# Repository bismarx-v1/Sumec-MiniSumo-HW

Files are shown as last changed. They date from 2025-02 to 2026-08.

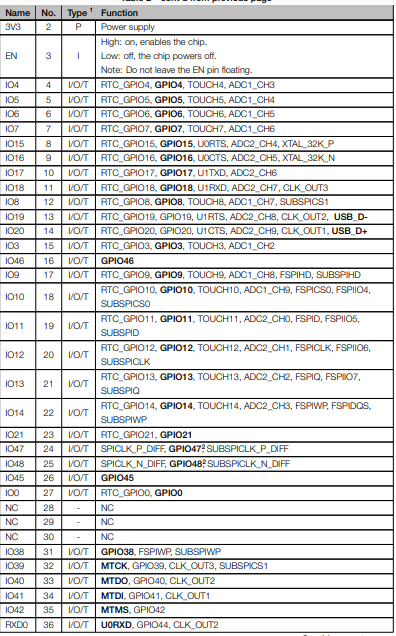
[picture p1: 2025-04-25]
main_hw/SUMEC_MK_II/REF. images/S3 pinout 1.png

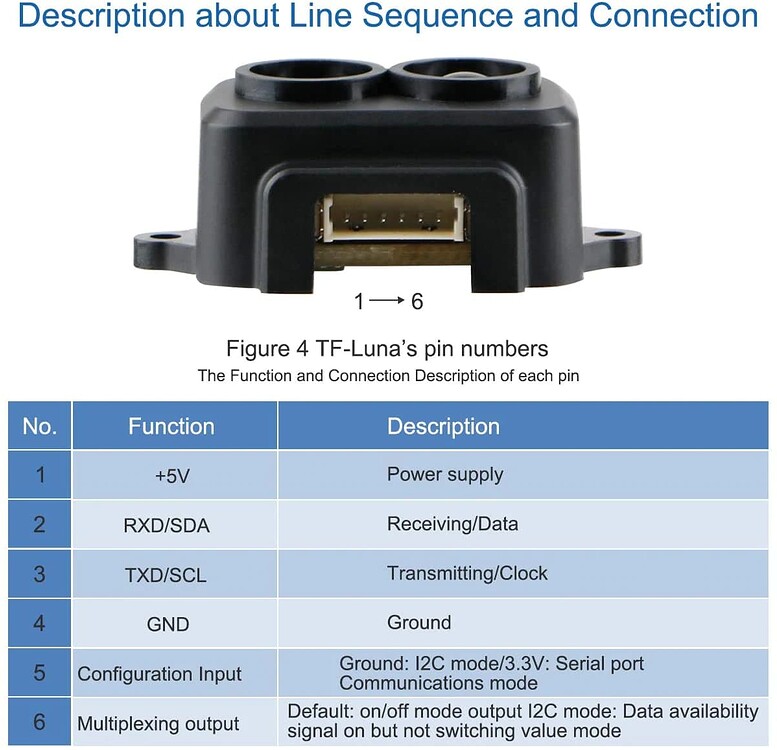
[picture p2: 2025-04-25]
main_hw/SUMEC_MK_II/REF. images/TF-Luna pinout.jpeg

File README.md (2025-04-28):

# SUMEC - HARDWARE - ELECTRONICS

**SUMEC** - is an autonomous MiniSumo robot, that is designed to compete in MiniSumo competitions. MiniSumo robots are small 100mmx100mm autonomous robots that combine electronics, software and mechanics into one project, their task it to push their opponent out of a ring. This project is led and managed by [SPŠ na Proseku](https://www.sps-prosek.cz) students.

## Table of Contents
- Description
- Contents
- Contributors
- Our Suppliers
- Contact
- Acknowledgements

## Description
This GitHub repository contains PCB files, gerber plots and main electronics used by SUMEC MiniSumo robot.

## Contents
- **main_hw**: Includes schematics and PCB files for the main board, production files such as Gerber plots and BOMs, .step files of the board, and PDF plots.
- **libs**: Contains needed libraries such as the footprint folder, 3D files in .step format, and the symbol library for schematics.

## Contributors
**HARDWARE Repository Supervisor**:
- **Savva Popov** - Head Hardware Developer and PCB Designer

**Project Contributors**:
- **Antonín Havlík** - Head Software Developer
- **Šimon Šťastný** - Head Mechanical Designer and Developer
- **Jonáš Jarý** - Mechanical Developer, Software and Hardware Development Assistant
- **Lukáš Houdek** - Mechanical Designer and Developer, 3D Printing Expert
- **Roselyn Natani Šimáčková** - Software developer, head functions developer

## Our Suppliers
We buy our components from:
- Mouser Electronics
- GM Electronics
- TME
- BotLand

## Contact
If you have any questions, suggestions, or issues regarding this project or repository, please feel free to contact:

### **Savva Popov** - Head Hardware Developer
  - Email: savva.popov.sp@gmail.com
  - LinkedIn: [Savva Popov](https://www.linkedin.com/in/savva-popov/)

### Other Contacts:
- **Antonín Havlík** - Head Software Developer
  - Email: [HAVLIK EMAIL]
- **Šimon Šťastný** - Head Mechanical Designer and Developer
  - Email: simon.ststn@gmail.com
- **Jonáš Jarý** - Mechanical Developer, Software and Hardware Development Assistant
  - Email: jary.jonas@gmail.com
- **Lukáš Houdek** - Mechanical Designer and Developer, 3D Printing Expert
  - Email: [HOUDEK EMAIL]
- **Roselyn Natani Šimáčková** - Software Developer, Head functions developer
  - Email: [SIMACKOVA EMAIL]

## Acknowledgements
We would like to thank Ing. Jaroslav Bušek PhD, for providing contacts and mentoring during the development of this project, and our school SPŠ na Proseku for providing workplace, knowledge, and top-notch equipment.

**Sending love from the Czech Republic!**

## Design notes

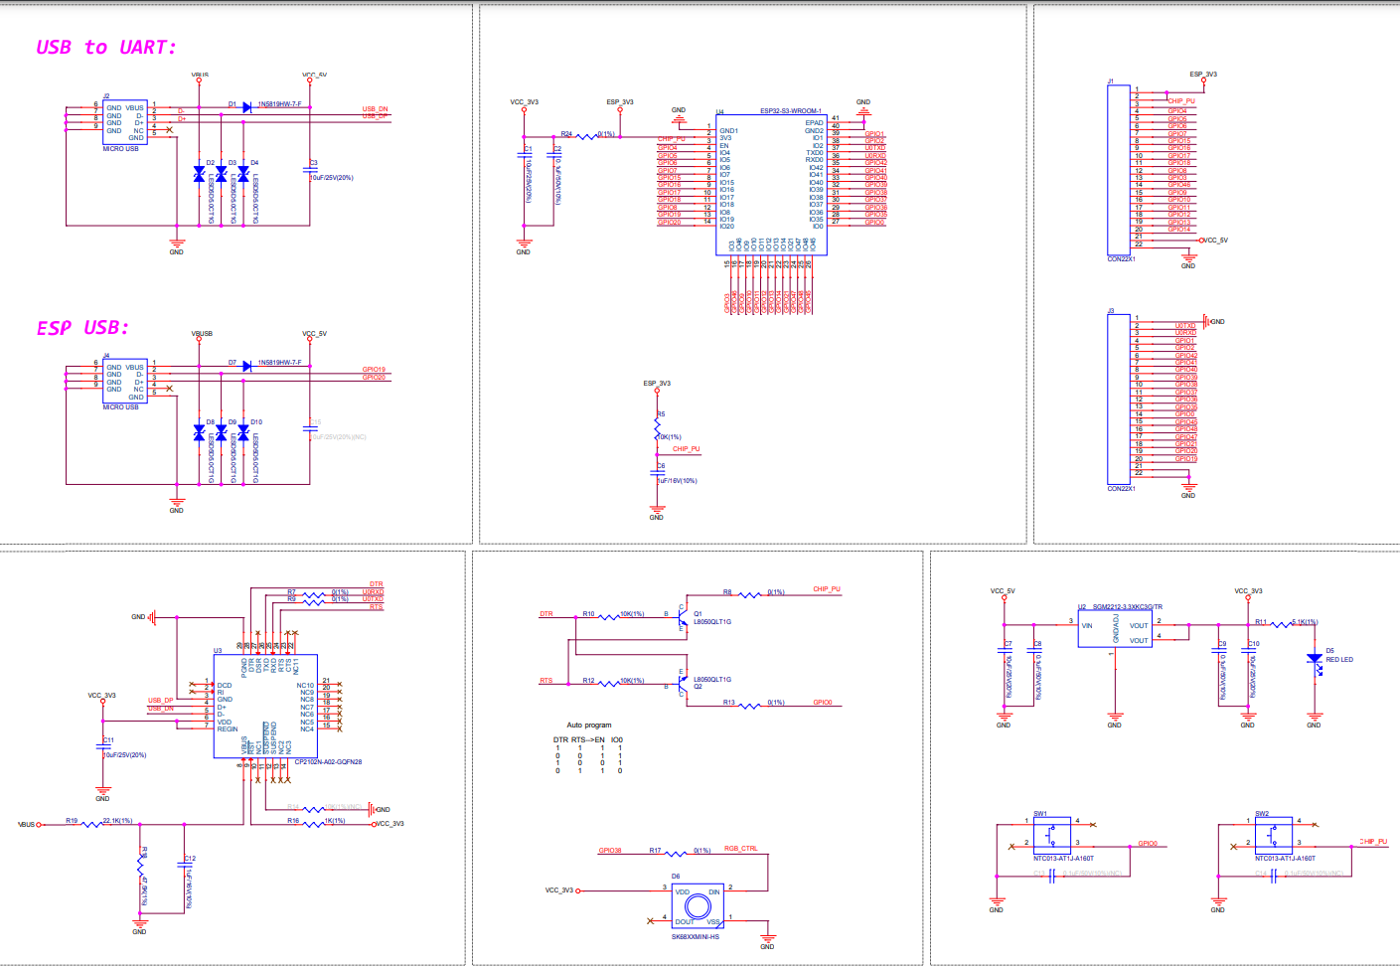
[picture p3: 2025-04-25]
main_hw/SUMEC_MK_II/REF. images/schematic S3 devboard.png

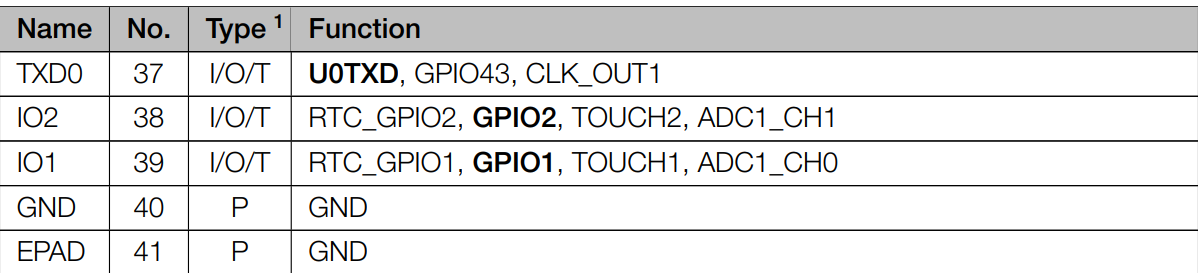
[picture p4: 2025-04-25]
main_hw/SUMEC_MK_II/REF. images/S3 pinout 2.png

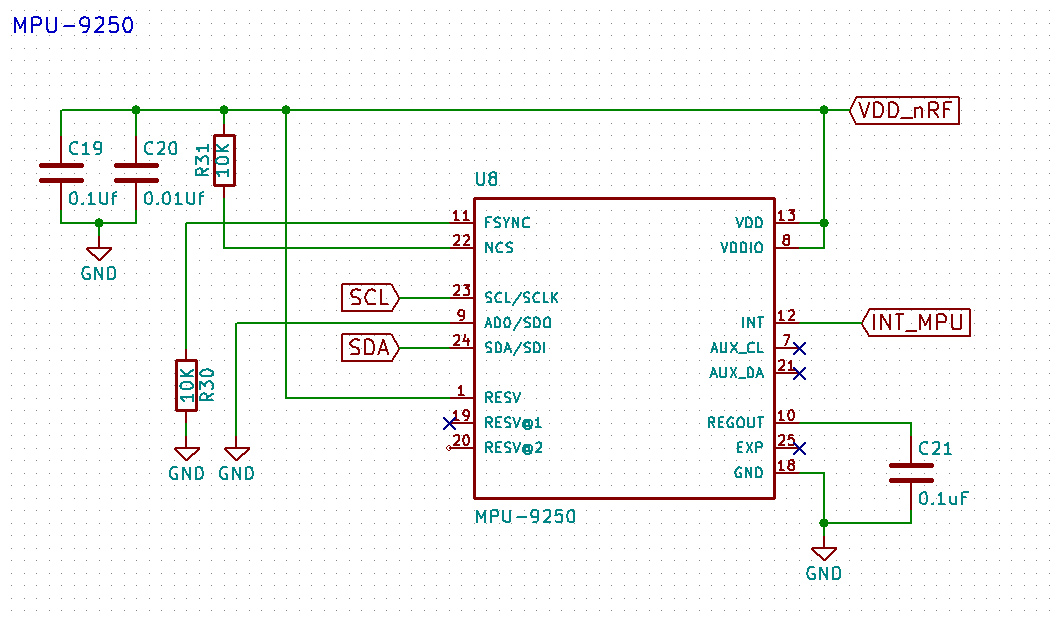
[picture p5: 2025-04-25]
main_hw/SUMEC_MK_II/REF. images/MPU-9250 schematic.png

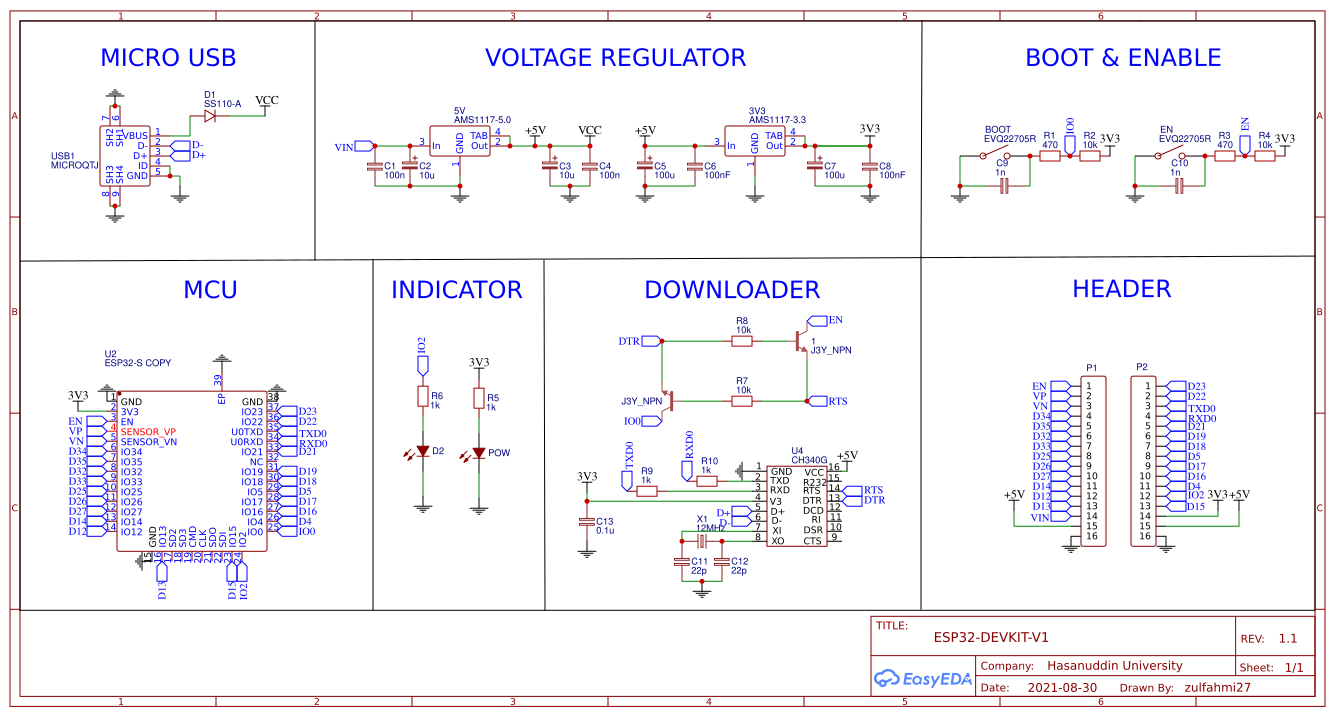
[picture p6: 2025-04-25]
main_hw/SUMEC_MK_II/REF. images/schematic 3.png

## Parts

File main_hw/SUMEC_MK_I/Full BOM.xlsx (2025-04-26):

QTY | VALUE | COMPONENT | COST | DO WE HAVE IT?
2 | 10uF | Cappacitor |  | 9
1 | RED | LED | 0 | YES
1 | D_Schottky | Diode |  | 2
3 | M3 | Mounting Hole |  | 30
1 | XT30U-F | Battery conneector |  | 2F and 2M
1 | 75 | Resistor
4 | 100 | Resistor |  | 6
4 | 10k | Resistor |  | 10
1 | SW_SPDT | Switch (3 pin header) |  | 2 types 8 in total
1 | SW_Push | Button | 0 | YES
1 | ESP32-DEVKIT-V1 | MCU |  | 3
3 | VL53L0X | Laser Sensor |  | 4
1 | TSOP382xx | IR Sensor |  | 1 module,
4 | QRE1113 | Line Rensor |  | 10 smd 11 thd
1 | LD1117AV33 | Stabiliastor |  | 2
1 | ROB-14450 | Motor Driver |  | 4+1
15x2 | 2,54mm | Pin Header
8x2 | 2,54mm | Pin Header
3 | CUSTOM MADE | Laser sensor connector
2 | 12V 150/300/500 RPM | DC Motors |  | 8
1 | 450mAh, 12,6V full charge | Battery/Terrorist battery |  | 1+1
2 | JSUMO | Silicon wheels |  | 3
2 | JSUMO/Custom made | Aluminuim wheels |  | 2+2
1 | Tester | Battery Tester |  | 1

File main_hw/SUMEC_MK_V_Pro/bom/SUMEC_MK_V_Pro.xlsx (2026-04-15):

Id | Designator | Footprint | Qty | Value | Link | Reserve
1 | C16, C17, C19, C20, C22, C23 | C_0805_2012Metric | 6 | 22u | 22uF, 16V, 0805, ceramic (https://cz.mouser.com/ProductDetail/Murata-Electronics/GRM21BR61C226ME44L?qs=H45D%252BQBid9ZSEksDj3jAIw%3D%3D)
2 | C9, C10, C11, C12, C14, C29 | C_0805_2012Metric | 6 | 10u | 10u, 16V, 0805, ceramic (https://cz.mouser.com/ProductDetail/Murata-Electronics/GRM21BZ71C106KE15K?qs=Ey7%2FXF42M3eyALzw2AAzwA%3D%3D)
3 | C25 | C_0805_2012Metric | 1 | 1u | 1uF, 25V, 0805, ceramic (https://cz.mouser.com/ProductDetail/Samsung-Electro-Mechanics/CL21B105KAFNFNE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)
4 | C1, C3, C5, C6, C7, C8, C13, C15, C18, C21, C24, C28, C30, C31 | C_0805_2012Metric | 14 | 100n | 100nF, 16V, 0805, ceramic (https://cz.mouser.com/ProductDetail/YAGEO/AC0805KRX7R7BB104)
5 | C2, C4 | C_0805_2012Metric | 2 | 22n | 22nF, 50V, 0805, ceramic, X7R (https://cz.mouser.com/ProductDetail/KYOCERA-AVX/08055C223KAT4A)
6 | C26, C27 | C_0805_2012Metric | 2 | 18p | 18pF, 50V, 0805, ceramic (https://cz.mouser.com/ProductDetail/Walsin/0805N180J500CT)
7 | R1 | R_0805_2012Metric | 1 | 2m | 2m, 500mW, 0805, yageo (https://cz.mouser.com/ProductDetail/YAGEO/PA0805FRE470R002L?qs=w%2Fv1CP2dgqowmpKkbnpTqw%3D%3D)
8 | R2, R3, R5, R7, R8, R14, R17, R20, R21, R22, R23, R24, R25, R26, R27, R29, R30, R36, R40 | R_0805_2012Metric | 19 | 10k | 10k, 250mW, 0805, vishay (https://cz.mouser.com/ProductDetail/Vishay-Dale/RCC080510K0FKEA?qs=GedFDFLaBXGY93oge9hajw%3D%3D)
9 | R4, R31 | R_0805_2012Metric | 2 | 2.2k | 2.2k, 125mW, 0805 (https://cz.mouser.com/ProductDetail/Panasonic/ERA-6AED222V?qs=MNPzkKEzRtSATzFNi%252BEAWg%3D%3D)
10 | R6, R11 | R_0805_2012Metric | 2 | 100k | 100k, 250mW, 0805, vishay (https://cz.mouser.com/ProductDetail/Vishay-Dale/RCC0805100KFKEA?qs=GedFDFLaBXFnw%2FnoDVfk4A%3D%3D)
11 | R9, R10 | R_0805_2012Metric | 2 | 5.1k | 5.23k, 125mW, 0805 (https://cz.mouser.com/ProductDetail/Panasonic/ERA-6AEB5231V)
12 | R12, R19 | R_0805_2012Metric | 2 | 52.3k | 52.3k, 125mW, 0805, vishay (https://cz.mouser.com/ProductDetail/Vishay-Dale/CRCW080552K3FKTA)
13 | R13 | R_0805_2012Metric | 1 | 45k | 45.3k, 125mW, 0805 vishay (https://cz.mouser.com/ProductDetail/Vishay-Dale/CRCW080545K3FKEA?qs=H9nSDuxQXAEd3s8xju4H0w%3D%3D)
14 | R15, R16 | R_0805_2012Metric | 2 | 15R | 15R, 100mW, 0805 panasonic (https://cz.mouser.com/ProductDetail/Panasonic/ERJ-6RED15R0V?qs=KTDjhDDUMAl6Ra4%2FZLG24g%3D%3D)
15 | R18 | R_0805_2012Metric | 1 | 100R | 100R, 250mW, 0805, vishay (https://cz.mouser.com/ProductDetail/Vishay-Dale/RCC0805100RFKEA?qs=GedFDFLaBXHpeG221Izd5g%3D%3D)
16 | R28 | R_0805_2012Metric | 1 | 0R | 0R. 250mW, 0805, vishay (https://cz.mouser.com/ProductDetail/Vishay-Dale/RCC08050000Z0EA?qs=GedFDFLaBXG1XappxO%252Bnuw%3D%3D)
17 | R32, R33, R34, R35, R37, R38, R39 | R_0805_2012Metric | 7 | 220R | 220R, 250mW, 0805 vishay (https://cz.mouser.com/ProductDetail/Vishay/RCC0805220RFKEA?qs=Imq1NPwxi74d31j49YrAMA%3D%3D)
18 | L1 | L_Vishay_IHLP-1616 | 1 | 3.3u | 3.3uH, 2.2A, 1616 (https://cz.mouser.com/ProductDetail/Vishay-Dale/IHLP1616BZER3R3M11?qs=gMuw6kkpPFjALKmObUci1A%3D%3D)
19 | L2 | L_Vishay_IHLP-1212 | 1 | 2.2u | 2.2uH, 2.3A, 0907 (https://cz.mouser.com/ProductDetail/ABRACON/AOTA-B252010S2R2MT?qs=1Kr7Jg1SGW8H59B6i%252B4XUg%3D%3D)
20 | D1, D2 | D_1206_3216Metric | 2 | D_Schottky | S-Diode, 2A, 1206, mouser (https://cz.mouser.com/ProductDetail/KYOCERA-AVX/SD1206S040S2R0?qs=jCA%252BPfw4LHbfEJl0sZ31oA%3D%3D) | Yellow LED, 20mA, 1.9V, 0805 (https://cz.mouser.com/ProductDetail/Stanley-Electric/FY1112H-TR?qs=byeeYqUIh0M%2F1I90%252BhjkXg%3D%3D)
21 | D3, D4, D5, D6, D7, D8, D9, D10, D11 | LED_0805_2012Metric | 9 | LED |  | Green LED, 20mA, 1.9V, 0805 (https://cz.mouser.com/ProductDetail/Stanley-Electric/VFHD1112H-3B72B-TR?qs=byeeYqUIh0N1xLw8fV03PA%3D%3D)
22 | U1 | HVSSOP-10-1EP_3x3mm_P0.5mm_EP1.83x1.89mm | 1 | INA226 | INA226AIDGSR (https://cz.mouser.com/ProductDetail/Texas-Instruments/INA226AIDGSR?qs=tQG3bEuiOZD4quG3egR36g%3D%3D) | Red LED, 20mA 1.9V, 0805 (https://cz.mouser.com/ProductDetail/Stanley-Electric/VFHV1112H-3BZ2B-TR?qs=byeeYqUIh0PKiA%252BYRcKo5Q%3D%3D)
23 | U2, U3 | DRV8874 | 2 | DRV8874PWPR | DRV8874 (https://cz.mouser.com/ProductDetail/Texas-Instruments/DRV8874PWPR?qs=mAH9sUMRCtvh%2FSU15ywmDA%3D%3D)
24 | U4 | SOT-563 | 1 | AP62300Z6 | AP62301Z6-7, 5V (https://cz.mouser.com/ProductDetail/Diodes-Incorporated/AP62301Z6-7?qs=7MVldsJ5UawPLFx7TLBzhA%3D%3D)
25 | U5 | SOT-563 | 1 | TPS565242DRLR | TPS565242DRLR, DC-DC 3.3V (https://cz.mouser.com/ProductDetail/Texas-Instruments/TPS565242DRLR?qs=tlsG%2FOw5FFgHUuabKshykA%3D%3D)
26 | U6 | TSOT-23-6 | 1 | USBLC6-2SC6 | ESD PROTECTION (https://cz.mouser.com/ProductDetail/STMicroelectronics/USBLC6-2SC6?qs=po45yt2pPpu%2FhNIlwQdTlg%3D%3D)
27 | U7 | LGA-28_5.2x3.8mm_P0.5mm | 1 | BNO055 | BNO055, IMU (https://cz.mouser.com/ProductDetail/Bosch-Sensortec/BNO055?qs=QhAb4EtQfbV8Z2YmISucWw%3D%3D)
28 | U8 | ESP32-S3-WROOM-1 | 1 | ESP32-S3-WROOM-1 | ESP32-WROOM-1-S3-N8 (https://cz.mouser.com/ProductDetail/Espressif-Systems/ESP32-S3-WROOM-1-N8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)
29 | U9 | SOT-23-5 | 1 | 24CW1280T-I/OT | 24CW1280T-I/OT EEPROM (https://cz.mouser.com/ProductDetail/Microchip-Technology/24CW1280T-I-OT?qs=qSfuJ%2Bfl%2Fd6lIWZGGRvkYA%3D%3D)
30 | Q1 | SOT-23-3 | 1 | PMOS | PMOS, 30V, 7.5A (https://cz.mouser.com/ProductDetail/Vishay-Semiconductors/SI2393DS-T1-GE3?qs=BJlw7L4Cy7%2FUF13oxTStOQ%3D%3D)
31 | BZ1 | BUZZER_CUI_CPT | 1 | Buzzer | Buzzer 80dB (https://cz.mouser.com/ProductDetail/CUI-Devices/CPT-1625-80-SMT-TR?qs=P1JMDcb91o43eCFIymFs3Q%3D%3D)
32 | Y1 | CM8V32768TA020125 | 1 | 32.768k | Crystal oscillator, 32.768kHz (https://cz.mouser.com/ProductDetail/Micro-Crystal/CM8V-T1A-32.768kHz-12.5pF-20PPM-TA-QC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)
33 | SW1 | Custom_SPDT_2.5_Switch | 1 | SW_DPDT_x2 | SPDT SW (https://cz.mouser.com/ProductDetail/Same-Sky/SLW-116641-5A-S-D?qs=IKkN%2F947nfBZSdW8n5Vqgw%3D%3D)
34 | SW2, SW3,SW4,SW5, SW6 | SW_SPST_EVQPE1 | 5 | BUTTON | Push button (https://cz.mouser.com/ProductDetail/Panasonic/EVQ-PE104K?qs=wX5mvoJE4NGLiYsCBZAptQ%3D%3D)
35 | J1 | XT30PW-M | 1 | XT30PW-M | XT30PW-M, TME (https://www.tme.eu/cz/details/xt30pw-m/konektory-dc/amass/)
36 | J2, J3 | JST_SH_BM06B-SRSS-TB_1x06-1MP_P1.00mm_Vertical | 2 | Conn_01x06_Socket | JST-SH, 6PIN, TME (https://www.tme.eu/cz/details/bm06b-srss-tb/signalove-konektory-raster-1-00mm/jst/bm06b-srss-tb-lf-sn/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)
37 | J4 | USB_C_Receptacle_GCT_USB4105-xx-A_16P_TopMnt_Horizontal | 1 | USB_C | USB-C Conn (https://eu.mouser.com/ProductDetail/GCT/USB4105-GF-A-060?qs=QNEnbhJQKvY2mocwNJzgfA%3D%3D)
38 | J5, J7, J8, J9, J10, J11 | Molex_PicoBlade_53398-0371_1x03-1MP_P1.25mm_Vertical | 6 | Conn_01x03_Pin | Molex PicoBlade, 3 Pin, vertical, mouser (https://eu.mouser.com/ProductDetail/Molex/53398-4003?qs=iLbezkQI%252BsgbJ%252BQuAD0UPA%3D%3D)
39 | J6 | Molex_PicoBlade_53398-0471_1x04-1MP_P1.25mm_Vertical | 1 | Conn_01x04_Pin | Molex PicoBlade, 4 Pin, vertical, mouser (https://eu.mouser.com/ProductDetail/Molex/53398-4004?qs=iLbezkQI%252Bsg1CAiQuTsV2g%3D%3D)
40 | J12 | Molex_PicoBlade_53398-0671_1x06-1MP_P1.25mm_Vertical | 1 | Conn_01x06_Pin | Molex PicoBlade, 6 Pin, vertical, mouser (https://eu.mouser.com/ProductDetail/Molex/53398-4006?qs=iLbezkQI%252BsgN7NG7c%2FlBfQ%3D%3D)
41 | J13 | TerminalBlock_Phoenix_MPT-0,5-3-2.54_1x03_P2.54mm_Horizontal | 1 | Conn_01x03_Pin

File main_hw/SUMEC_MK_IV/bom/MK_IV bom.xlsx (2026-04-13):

Designator | Footprint | Quantity | Value | Link | Reserve | Quantity
A1 | ESP32-WROOM32 | 4 | ESP32-WROOM-32E-N16 | ESP32E - Natani (https://cz.mouser.com/ProductDetail/Espressif-Systems/ESP32-WROOM-32E-N16?qs=Li%2BoUPsLEnsC4cA%2BUYB2Bw%3D%3D)
C1 | C_0805_2012Metric_Pad1.18x1.45mm_HandSolder | 1 | 3.3nF | 3.3nF, 16V, 0805, X7R (https://cz.mouser.com/ProductDetail/KYOCERA-AVX/0805YC332MAT2A?qs=0N%252Bs6Hre8enahhqbMno5oA%3D%3D)
C11,C13 | C_0805_2012Metric_Pad1.18x1.45mm_HandSolder | 2 | 22nF | 22nF, 50V, 0805, ceramic, X7R (https://cz.mouser.com/ProductDetail/KYOCERA-AVX/08055C223KAT4A)
C3,C17,C19,C24,C18,C25 | CP_EIA-3216-18_Kemet-A_Pad1.58x1.35mm_HandSolder | 6 | 10uF | 10uF, 16V, 1206, tantal (https://cz.mouser.com/ProductDetail/KEMET/T491A106K016AT) | 28
C4,C5,C16,C15,C10,C21,C23,C22,C12,C14,C20 | C_0805_2012Metric_Pad1.18x1.45mm_HandSolder | 11 | 100nF | 100nF, 16V, 0805, ceramic, X7R (https://cz.mouser.com/ProductDetail/YAGEO/AC0805KRX7R7BB104) | >60
C9,C6,C7,C8,C2 | CP_EIA-2012-12_Kemet-R_Pad1.30x1.05mm_HandSolder | 5 | 22uF | 22uF, 10V, 0805, tantalum (https://cz.mouser.com/ProductDetail/KYOCERA-AVX/TCTP1A226M8R?qs=By6Nw2ByBD3AJs9Xk0HVmg%3D%3D)
D2,D1 | D_1206_3216Metric_Pad1.42x1.75mm_HandSolder | 2 | D_Schottky | S-Diode, 2A, 1206, mouser (https://cz.mouser.com/ProductDetail/KYOCERA-AVX/SD1206S040S2R0?qs=jCA%252BPfw4LHbfEJl0sZ31oA%3D%3D) | 1
D4,D5,D7,D6 | LED_0805_2012Metric_Pad1.15x1.40mm_HandSolder | 4 | LED
 |  |  | Y_LED | Yellow LED, 20mA, 1.9V, 0805 (https://cz.mouser.com/ProductDetail/Stanley-Electric/FY1112H-TR?qs=byeeYqUIh0M%2F1I90%252BhjkXg%3D%3D) | 6
 |  |  | G_LED | Green LED, 20mA, 1.9V, 0805 (https://cz.mouser.com/ProductDetail/Stanley-Electric/VFHD1112H-3B72B-TR?qs=byeeYqUIh0N1xLw8fV03PA%3D%3D) | 4
 |  |  | R_LED | Red LED, 20mA 1.9V, 0805 (https://cz.mouser.com/ProductDetail/Stanley-Electric/VFHV1112H-3BZ2B-TR?qs=byeeYqUIh0PKiA%252BYRcKo5Q%3D%3D) | 15
F1 | Fuse_1206_3216Metric_Pad1.42x1.75mm_HandSolder | 1 | Polyfuse/50R | Polyfuse, Itrip 500mA, 16V (https://cz.mouser.com/ProductDetail/Littelfuse/0805L020-16YR?qs=HoCaDK9Nz5e9OjGjdp4q0Q%3D%3D) | 0
IC1 | SOT-563 | 1 | TPS565242DRLR | TPS565242DRLR, 3V3 OUTPUT (https://cz.mouser.com/ProductDetail/Texas-Instruments/TPS565242DRLR?qs=tlsG%2FOw5FFgHUuabKshykA%3D%3D) | 0
IC2,IC3 | DRV8874 | 2 | DRV8874PWPR | DRV8874 (https://cz.mouser.com/ProductDetail/Texas-Instruments/DRV8874PWPR?qs=mAH9sUMRCtvh%2FSU15ywmDA%3D%3D) | 0
J1 | XT30PW-M | 1 | XT30PW-M | XT30PW-M, TME (https://www.tme.eu/cz/details/xt30pw-m/konektory-dc/amass/) | 0
J12,J14 | JST_SH_BM06B-SRSS-TB_1x06-1MP_P1.00mm_Vertical | 2 | Conn_01x06_Socket | JST-SH, 6PIN, TME (https://www.tme.eu/cz/details/bm06b-srss-tb/signalove-konektory-raster-1-00mm/jst/bm06b-srss-tb-lf-sn/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) | 0
J2 | USB_Type_C | 1 | USB_TypeC | USB-C Conn (https://eu.mouser.com/ProductDetail/GCT/USB4105-GF-A-060?qs=QNEnbhJQKvY2mocwNJzgfA%3D%3D) | 4
J3,J4,J7 | Molex_PicoBlade_53398-0671_1x06-1MP_P1.25mm_Vertical | 3 | Conn_01x06_Pin | Molex PicoBlade, 6 Pin, vertical, mouser (https://eu.mouser.com/ProductDetail/Molex/53398-4006?qs=iLbezkQI%252BsgN7NG7c%2FlBfQ%3D%3D) | 1
J6,J11,J9,J10,J13,J5 | Molex_PicoBlade_53398-0371_1x03-1MP_P1.25mm_Vertical | 6 | Conn_01x03_Pin | Molex PicoBlade, 3 Pin, vertical, mouser (https://eu.mouser.com/ProductDetail/Molex/53398-4003?qs=iLbezkQI%252BsgbJ%252BQuAD0UPA%3D%3D) | 4
J8 | Molex_PicoBlade_53398-0471_1x04-1MP_P1.25mm_Vertical | 1 | Conn_01x04_Pin | Molex PicoBlade, 4 Pin, vertical, mouser (https://eu.mouser.com/ProductDetail/Molex/53398-4004?qs=iLbezkQI%252Bsg1CAiQuTsV2g%3D%3D) | 2
L1 | L_Vishay_IHLP-1212 | 1 | 1.5uH | 1.5uH 1212 (https://cz.mouser.com/ProductDetail/Vishay-Dale/IHLP1212BZEV1R5M5A?qs=BJlw7L4Cy7%2FLPKyjRWwgFw%3D%3D)
L2 | L_Vishay_IHLP-1616 | 1 | 2.2uH | 2.2uH 1616 (https://cz.mouser.com/ProductDetail/Vishay-Dale/IHLP1616BZER2R2M5A?qs=AQlKX63v8Rsr6Hc3BY6yZA%3D%3D)
Q1,Q2 | SOT-23-3 | 2 | Q_PMOS | PMOS VGS 16V (https://cz.mouser.com/ProductDetail/Vishay-Semiconductors/SI2393DS-T1-GE3?qs=BJlw7L4Cy7%2FUF13oxTStOQ%3D%3D)
R1,R4,R14,R2,R8,R9,R19 | R_0805_2012Metric_Pad1.20x1.40mm_HandSolder | 7 | 10k | 10k, 250mW, 0805, vishay (https://cz.mouser.com/ProductDetail/Vishay-Dale/RCC080510K0FKEA?qs=GedFDFLaBXGY93oge9hajw%3D%3D) | <60
R6,R7,R10,R11 | R_0805_2012Metric_Pad1.20x1.40mm_HandSolder | 4 | 0R | 0R. 250mW, 0805, vishay (https://cz.mouser.com/ProductDetail/Vishay-Dale/RCC08050000Z0EA?qs=GedFDFLaBXG1XappxO%252Bnuw%3D%3D)
R13,R12 | R_0805_2012Metric_Pad1.20x1.40mm_HandSolder | 2 | 15R | 15R, 100mW, 0805 panasonic (https://cz.mouser.com/ProductDetail/Panasonic/ERJ-6RED15R0V?qs=KTDjhDDUMAl6Ra4%2FZLG24g%3D%3D) | 16
R15 | R_0805_2012Metric_Pad1.20x1.40mm_HandSolder | 1 | 560R | 560R, 500mW, 0805, bourns (https://cz.mouser.com/ProductDetail/Bourns/CHP0805AFX-5600ELF?qs=GedFDFLaBXHiLkJv9wkGiw%3D%3D) | 18
R18,R17,R16,R20 | R_0805_2012Metric_Pad1.20x1.40mm_HandSolder | 4 | 100R | 100R, 250mW, 0805, vishay (https://cz.mouser.com/ProductDetail/Vishay-Dale/RCC0805100RFKEA?qs=GedFDFLaBXHpeG221Izd5g%3D%3D) | 10
R3 | R_0805_2012Metric_Pad1.20x1.40mm_HandSolder | 1 | 45k | 45.3k, 125mW, vishay (https://cz.mouser.com/ProductDetail/Vishay-Dale/CRCW080545K3FKEA?qs=H9nSDuxQXAEd3s8xju4H0w%3D%3D)
R5 | R_0805_2012Metric_Pad1.20x1.40mm_HandSolder | 1 | 100k | 100k, 250mW, 0805, vishay (https://cz.mouser.com/ProductDetail/Vishay-Dale/RCC0805100KFKEA?qs=GedFDFLaBXFnw%2FnoDVfk4A%3D%3D)
SW1 | Custom_SPDT_2.5_Switch | 1 | SW_DPDT_x2 | SPDT SW (https://cz.mouser.com/ProductDetail/Same-Sky/SLW-116641-5A-S-D?qs=IKkN%2F947nfBZSdW8n5Vqgw%3D%3D)
SW3,SW4,SW2,SW5 | SW_SPST_EVQPE1 | 4 | SW_Push | Push button (https://cz.mouser.com/ProductDetail/Panasonic/EVQ-PE104K?qs=wX5mvoJE4NGLiYsCBZAptQ%3D%3D)
U1 | VQFN-16-1EP_3x3mm_P0.5mm_EP1.68x1.68mm_ThermalVias | 1 | TPS62133 | TPS62133 5V OUTPUT (https://cz.mouser.com/ProductDetail/Texas-Instruments/TPS62133RGTR?qs=gXEV9p%2FxLgfynMj9v6Z0Jw%3D%3D)
U2 | ESP32-S3-WROOM-1 | 1 | ESP32-S3-WROOM-1 | ESP32-WROOM-1-S3-N8 (https://cz.mouser.com/ProductDetail/Espressif-Systems/ESP32-S3-WROOM-1-N8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) | 1
U3 | TSOT-23-6_HandSoldering | 1 | USBLC6-2SC6 | ESD PROT | 6
U4 | Vishay_TSOP382 | 1 | TSOP382xx | TSOP382 (https://cz.mouser.com/ProductDetail/Vishay-Semiconductors/TSOP38238?qs=RzxYCzJDjPVjpHVZS582Ng%3D%3D)
 |  | 3 |  | MolexPicoblade, 3pin, Female (https://cz.mouser.com/ProductDetail/Molex/51021-0300?qs=u6Gr9%2FNt%252B%2F8RVcr%252BZnBcoQ%3D%3D)
 |  | 2 |  | MolexPicoblade, 4pin, Female (https://cz.mouser.com/ProductDetail/Molex/51021-0400?qs=ILqg114nvd6Z%252BmZXFEtu8g%3D%3D)
 |  | 6 |  | MolexPicoblade, 6pin Female (https://cz.mouser.com/ProductDetail/Molex/51021-0600?qs=ZwgtpdmWYYSz82DH2HMXiQ%3D%3D)
 |  | 100 |  | MolexPicoblade Crimp chain (https://cz.mouser.com/ProductDetail/Molex/50079-8001?qs=rQFj71Wb1eU%2F0jEbXbt8Hg%3D%3D)
 |  |  |  | LM1084 5V LDO Reg (https://cz.mouser.com/ProductDetail/Texas-Instruments/LM1084ISX-5.0-NOPB?qs=X1J7HmVL2ZHZhBfW33wzFQ%3D%3D)
 |  |  |  | USB-C Conn (https://eu.mouser.com/ProductDetail/GCT/USB4105-GF-A-060?qs=QNEnbhJQKvY2mocwNJzgfA%3D%3D) | 640-USB4105-GF-A-060
 |  |  |  | Button (https://cz.mouser.com/ProductDetail/Omron-Electronics/B3U-1000P?qs=AO7BQMcsEu4ip80xyf2FwA%3D%3D) | 653-B3U-1000P
 |  |  |  | TPS62133 5V OUTPUT (https://cz.mouser.com/ProductDetail/Texas-Instruments/TPS62133RGTR?qs=gXEV9p%2FxLgfynMj9v6Z0Jw%3D%3D) | 595-TPS62133RGTR
 |  |  |  | NCP1117 (https://cz.mouser.com/ProductDetail/onsemi/NCP1117ST33T3G?qs=Gev%252BmEvV0iZb%2FE8ahUDx3w%3D%3D) | 863-NCP1117ST33T3G
 |  |  |  | SD-Card (https://cz.mouser.com/ProductDetail/GCT/MEM2067-02-180-00-A?qs=KUoIvG%2F9IlYTw%2Fcc1GlNJA%3D%3D) | 640-MEM20670218000A
 |  |  |  | Polyfuse, Itrip 500mA, 16V (https://cz.mouser.com/ProductDetail/Littelfuse/0805L020-16YR?qs=HoCaDK9Nz5e9OjGjdp4q0Q%3D%3D) | 576-0805L020/16YR

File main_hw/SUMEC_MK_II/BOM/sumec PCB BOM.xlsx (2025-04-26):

 | 58
Item | Qty | Reference(s) | Value | LibPart | Footprint | Link
1 | 1 | C1 | 10uF.hb | Kondenzator elektrolyt. | Capacitor_SMD:C_1206_3216Metric | Tantal. 10uF, 25V mouser (https://cz.mouser.com/ProductDetail/KYOCERA-AVX/TCJA106M025R0150E?qs=hWgE7mdIu5SUx0aLKy2TqQ%3D%3D)
2 | 1 | C2 | 1uF.hb | Kondenzator elektrolyt. | Capacitor_SMD:C_1206_3216Metric | Tantal, 1uf 16V mouser (https://cz.mouser.com/ProductDetail/KEMET/T491A105K016AT?qs=rZB7yXOqaoskTND3m0TpXQ%3D%3D)
3 | 1 | C3 | 10uF.mcu | Kondenzator | Capacitor_SMD:C_1206_3216Metric | 10uF 16V mouser (https://cz.mouser.com/ProductDetail/KYOCERA-AVX/KAF31GR71C106KU)
4 | 1 | C4 | 100nF.mcu | Kondenzator | Capacitor_SMD:C_1206_3216Metric | 0,1uF 25V (https://cz.mouser.com/ProductDetail/KYOCERA-AVX/12063C104JAT2A?qs=R2iZg1vr0omiyJ4oLGXaVA%3D%3D)
5 | 1 | C5 | 10uF.hbc | Kondenzator | Capacitor_SMD:C_1206_3216Metric | 10uF 16V mouser (https://cz.mouser.com/ProductDetail/KYOCERA-AVX/KAF31GR71C106KU)
6 | 1 | C6 | 100nF.hbc | Kondenzator | Capacitor_SMD:C_1206_3216Metric | 0,1uF 25V (https://cz.mouser.com/ProductDetail/KYOCERA-AVX/12063C104JAT2A?qs=R2iZg1vr0omiyJ4oLGXaVA%3D%3D)
7 | 1 | C7 | 100nF.en | Kondenzator | Capacitor_SMD:C_1206_3216Metric | 0,1uF 25V (https://cz.mouser.com/ProductDetail/KYOCERA-AVX/12063C104JAT2A?qs=R2iZg1vr0omiyJ4oLGXaVA%3D%3D)
8 | 1 | C8 | 100nF.boot | Kondenzator | Capacitor_SMD:C_1206_3216Metric | 0,1uF 25V
9 | 1 | C9 | 100nF | Kondenzator | Capacitor_SMD:C_1206_3216Metric | 0,1uF 25V
10 | 4 | C10, C11, C12, C13 | 10uF.stabl | Kondenzator | Capacitor_SMD:C_1206_3216Metric_Pad1.33x1.80mm_HandSolder | 10uF 16V mouser (https://cz.mouser.com/ProductDetail/KYOCERA-AVX/KAF31GR71C106KU)
11 | 1 | D1 | 1N5819 | Schottkyeho dioda | Diode_SMD:D_1206_3216Metric | Schottkyho dioda 1206 2A propustny proud (https://cz.mouser.com/ProductDetail/Bourns/CD1206-B260?qs=VNGG2InBe5GH7Tt0gN3c%2FQ%3D%3D)
12 | 4 | H1, H2, H3, H4 | MountingHole M3 | Montažní otvor | MountingHole:MountingHole_3.2mm_M3
13 | 1 | IC1 | XT30U-F | XT-30 | sumec_library:AMASS_XT30U-M_1x02_P5.0mm_Vertical
14 | 1 | J1 | Conn_01x04_Pin | Dutinková lišt | Connector_PinHeader_2.54mm:PinHeader_1x04_P2.54mm_Vertical
15 | 1 | J2 | Conn_01x01_Pin | Dutinková lišt | Connector_Wire:SolderWire-0.1sqmm_1x01_D0.4mm_OD1mm
16 | 1 | J3 | Conn_01x03_Pin | Dutinková lišt | Connector_PinSocket_2.54mm:PinSocket_1x03_P2.54mm_Vertical
17 | 1 | J4 | USB | USB Type-C | sumec-smd_library:HRO_TYPE-C-31-M-12 | USB C mouser (https://cz.mouser.com/ProductDetail/GCT/USB4105-GF-A-060?qs=QNEnbhJQKvY2mocwNJzgfA%3D%3D&mgh=1)
18 | 3 | J5, J6, J7 | Conn_01x06_Pin | JST-SH 6 pin female | Connector_JST:JST_SH_BM06B-SRSS-TB_1x06-1MP_P1.00mm_Vertical | JST SH 6 pin 1mm dratek (https://dratek.cz/arduino/122193-jst-sh-1.0mm-6-pin-konektor-na-dps-rovny.html)
19 | 1 | J8 | Conn_01x02 | Connector_Generic:Conn_01x02 | Connector_PinHeader_2.54mm:PinHeader_1x02_P2.54mm_Vertical
20 | 1 | JP1 | SolderJumper_3_Open | PROPOJKA | Jumper:SolderJumper-3_P2.0mm_Open_TrianglePad1.0x1.5mm
21 | 1 | R1 | LOGO | Rezistor | sumec-smd_library:logo even smaller
22 | 1 | R2 | LOGO | Rezistor | sumec-smd_library:car cool smol
23 | 7 | R3, R7, R8, R9, R10, R11, R12 | 0R | Rezistor | Resistor_SMD:R_1206_3216Metric | 0R mouser (https://cz.mouser.com/ProductDetail/Vishay-Dale/CRCW12060000ZSTC?qs=y5m63dMNjqu0KlgPSWR0ZQ%3D%3D)
24 | 2 | R4, R5 | 15R | Rezistor | Resistor_SMD:R_1206_3216Metric | 15R mouser (https://cz.mouser.com/ProductDetail/YAGEO/AC1206JR-0715RL?qs=sGAEpiMZZMtlubZbdhIBIH9nMdKz1PS4dnbbMPYu1PU%3D)
25 | 1 | R6 | 10k.mcu | Rezistor | Resistor_SMD:R_1206_3216Metric | 10k mouser (https://cz.mouser.com/ProductDetail/Panasonic/ERA-8VRB1002V?qs=sGAEpiMZZMtlubZbdhIBINZaoL9yqB51I6UW8FwQKMs%3D)
26 | 3 | R13, R15, R17 | 100R | Rezistor | Resistor_SMD:R_1206_3216Metric | 100R mouser (https://cz.mouser.com/ProductDetail/YAGEO/RT1206BRD07100RL?qs=Br90QIIERxRNyANs6F674w%3D%3D)
27 | 3 | R14, R16, R18 | 10k | Rezistor | Resistor_SMD:R_1206_3216Metric | 10k mouser (https://cz.mouser.com/ProductDetail/Panasonic/ERA-8VRB1002V?qs=sGAEpiMZZMtlubZbdhIBINZaoL9yqB51I6UW8FwQKMs%3D)
28 | 3 | SW1, SW3, SW4 | SW_Push | Tlačitko | Button_Switch_SMD:SW_SPST_B3U-1000P | B3U-1000P mouser (https://cz.mouser.com/ProductDetail/Omron-Electronics/B3U-1000P?qs=AO7BQMcsEu4ip80xyf2FwA%3D%3D)
29 | 1 | U1 | TB6612FNG | H-můstek | Package_SO:SSOP-24_5.3x8.2mm_P0.65mm | TB6612FNG mouser (https://cz.mouser.com/ProductDetail/Toshiba/TB6612FNGC8EL?qs=rsevcuukUAy2UalRuv4E%2FQ%3D%3D)
30 | 1 | U2 | ESP32-S3-WROOM-1 | Čip | PCM_Espressif:ESP32-S3-WROOM-1 | ESP32 S3 WROOM1 mouser (https://cz.mouser.com/ProductDetail/Espressif-Systems/ESP32-S3-WROOM-1-N4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)
31 | 1 | U3 | USBLC6-2SC6 | ESD Protekce | Package_TO_SOT_SMD:TSOT-23-6_HandSoldering | ESD protekce mouser (https://cz.mouser.com/ProductDetail/STMicroelectronics/USBLC6-2SC6?qs=po45yt2pPpu%2FhNIlwQdTlg%3D%3D)
32 | 1 | U4 | TSOP382xx | IR LEDka | Connector_PinSocket_2.54mm:PinSocket_1x03_P2.54mm_Vertical | TSOP382. 38kHz mouser (https://cz.mouser.com/ProductDetail/Vishay-Semiconductors/TSOP38238?qs=RzxYCzJDjPVjpHVZS582Ng%3D%3D)
33 | 3 | U5, U6, U7 | QRE1113 | Senzor čarý | sumec_library:OnSemi_CASE100AQ - QRE1113 | QRE1113 THT mouser (https://cz.mouser.com/ProductDetail/onsemi-Fairchild/QRE1113?qs=ne66E0WZ%2FFkJiYCW1J5zEw%3D%3D)
34 | 1 | U8 | LM1084IS-5.0/NOPB | Stabilizator | Package_TO_SOT_SMD:TO-252-3_TabPin2 | TO-252-3, 1,5A, 5Vout, 25Vmax mouser (https://cz.mouser.com/ProductDetail/Nisshinbo/NJM7805SDL1-TE1?qs=GBLSl2AkirtxkrsaOjZilw%3D%3D)
35 | 1 | U9 | LM1084IS-3.3/NOPB | Stabilizator | Package_TO_SOT_SMD:TO-252-3_TabPin2 | TO-252-3, 1,5A, 3.3Vout, 13Vmax mouser (https://cz.mouser.com/ProductDetail/STMicroelectronics/LD29150DT33R?qs=M4RLcaOHglr1iYLz8rxZ4g%3D%3D)

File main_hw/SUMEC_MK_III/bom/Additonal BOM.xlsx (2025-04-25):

Id | Designator | Qty | Footprint | Value | Link | Reserve | Quantity to order
1 | J8,J7 | 2 | SHARP1-2, 3PIN | Conn_01x03_Pin | PicoBlade, 3P, 75mm, Female to Blunt (https://cz.mouser.com/ProductDetail/Molex/218112-0300?qs=QNEnbhJQKva%2Fzwq48R2atA%3D%3D) |  | 6
2 | J10 | 1 | QRE SNGL, 3PIN | Conn_01x03_Pin | PicoBlade, 3P, 75mm, Female to Blunt (https://cz.mouser.com/ProductDetail/Molex/218112-0300?qs=QNEnbhJQKva%2Fzwq48R2atA%3D%3D)
3 | J9 | 1 | MAIN BRD TO QRE MINIBRD MALE, 4PIN | Conn_01x04_Pin | PicoBlade, 4P, 100mm, Female to Female (https://cz.mouser.com/ProductDetail/Molex/15134-0401?qs=lQAVKuKFhkKhGB2D3%252BUAcg%3D%3D) |  | 2
4 | J5,J4,J6 | 3 | TF-LUNA, MALE, 6PIN | Conn_01x06_Pin | PicoBlade, 6P, 100mm Female to Female (https://cz.mouser.com/ProductDetail/Molex/15134-0601?qs=lQAVKuKFhkKZ3d51CS44yQ%3D%3D) |  | 6
5 | SW2 | 1 | Custom_SPDT_4.8mm_Switch | SW_DPDT_x2 | SPDT Switch (https://cz.mouser.com/ProductDetail/E-Switch/500SSP3S4M6QEB?qs=f57gQzlyLip2q9oLHFusmQ%3D%3D) |  | 2

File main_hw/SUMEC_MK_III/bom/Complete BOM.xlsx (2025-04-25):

Id | Designator | Quantity | Footprint | Value | Link | Reserve | Quantity
1 | R3 | 1 | R_0805_2012Metric_Pad1.20x1.40mm_HandSolder | 560R | 560R, 500mW, 0805, mouser (https://cz.mouser.com/ProductDetail/Bourns/CHP0805AFX-5600ELF?qs=GedFDFLaBXHiLkJv9wkGiw%3D%3D) | 20 | 1
2 | R5 | 1 | R_1206_3216Metric_Pad1.30x1.75mm_HandSolder | 0R | 0R, 250mW, 1206, mouser (https://cz.mouser.com/ProductDetail/Vishay-Dale/CRCW12060000ZSTC?qs=y5m63dMNjqu0KlgPSWR0ZQ%3D%3D) | 14 | 1
3 | R7,R6 | 2 | R_0805_2012Metric_Pad1.20x1.40mm_HandSolder | 15R | 15R, 100mW, 0805,mouser (https://cz.mouser.com/ProductDetail/Panasonic/ERJ-6RED15R0V?qs=KTDjhDDUMAl6Ra4%2FZLG24g%3D%3D) | 20 | 2
4 | R9,R8 - R4,R2 | 4 | R_0805_2012Metric_Pad1.20x1.40mm_HandSolder | 10k | 10k, 250mW, 0805, mouser (https://cz.mouser.com/ProductDetail/Vishay-Dale/RCC080510K0FKEA?qs=GedFDFLaBXGY93oge9hajw%3D%3D) | 20 | 4
5 | R1,R2,R10 - R3,R1 | 5 | R_0805_2012Metric_Pad1.20x1.40mm_HandSolder | 100R | 100R, 0.5W, 0805, mouser (https://cz.mouser.com/ProductDetail/Vishay-Dale/CRCW0805100RFKEAHP?qs=k2%2FDWSARqgHN0DmoUSjg4g%3D%3D) | 20 | 5
6 | R20, R21 | 2 | R2D2, Logo | R |  |  | 2
7 | C3,C4 | 2 | C_0805_2012Metric_Pad1.18x1.45mm_HandSolder | 22nF.hb | 22nF, 50V, 0805, ceramic, mouser, X7R (https://cz.mouser.com/ProductDetail/KYOCERA-AVX/08055C223KAT4A) | 20 | 2
8 | C2,C13,C5,C6,C7,C8,C11,C12 | 8 | C_0805_2012Metric_Pad1.18x1.45mm_HandSolder | 100nF | 100nF, 16V, 0805, ceramic, mouser X7R (https://cz.mouser.com/ProductDetail/YAGEO/AC0805KRX7R7BB104) | 100? | 8
9 | C1,C9,C10,C15,C14,C19,C17,C18,C16 | 9 | CP_EIA-3216-18_Kemet-A_Pad1.58x1.35mm_HandSolder | 10uF | 10uF, 16V, 1206, tantal, mouser (https://cz.mouser.com/ProductDetail/KEMET/T491A106K016AT) | 50? | 9
10 | D1 | 1 | LED_0805_2012Metric_Pad1.15x1.40mm_HandSolder | LED | Red LED, 20mA 1.9V, 0805, mouser (https://cz.mouser.com/ProductDetail/Stanley-Electric/VFHV1112H-3BZ2B-TR?qs=byeeYqUIh0PKiA%252BYRcKo5Q%3D%3D) | 10 | 1
11 | D2 | 1 | LED_0805_2012Metric_Pad1.15x1.40mm_HandSolder | LED | Yellow LED, 20mA, 1.9V, 0805, mouser (https://cz.mouser.com/ProductDetail/Stanley-Electric/FY1112H-TR?qs=byeeYqUIh0M%2F1I90%252BhjkXg%3D%3D) | 10 | 1
12 | D4 | 1 | LED_0805_2012Metric_Pad1.15x1.40mm_HandSolder | LED | Green-Yellow LED, 20mA, 1.9V, mouser (https://cz.mouser.com/ProductDetail/Stanley-Electric/VFHD1112H-3B72B-TR?qs=byeeYqUIh0N1xLw8fV03PA%3D%3D) | 20 | 1
13 | D3 | 1 | D_1206_3216Metric_Pad1.42x1.75mm_HandSolder | D_Schottky | S-Diode, 2A, 1206, mouser (https://cz.mouser.com/ProductDetail/KYOCERA-AVX/SD1206S040S2R0?qs=jCA%252BPfw4LHbfEJl0sZ31oA%3D%3D) | 6 | 1
14 | J1 | 1 | JST_XH_B4B-XH-A_1x04_P2.50mm_Vertical | Conn_01x04_Pin |  |  | 1
15 | J2 | 1 | SolderWire-0.1sqmm_1x01_D0.4mm_OD1mm | Conn_01x01_Pin |  |  | 1
16 | J9 | 1 | Molex_PicoBlade_53398-0471_1x04-1MP_P1.25mm_Vertical | Conn_01x04_Pin | Molex PicoBlade, 4 Pin, vertical, mouser (https://cz.mouser.com/ProductDetail/Molex/53398-4004?qs=iLbezkQI%252Bsg1CAiQuTsV2g%3D%3D) | 4 | 1
17 | J10,J8,J7 | 3 | Molex_PicoBlade_53398-0371_1x03-1MP_P1.25mm_Vertical | Conn_01x03_Pin | Molex PicoBlade, 3 Pin, vertical, mouser (https://cz.mouser.com/ProductDetail/Molex/53398-4003?qs=iLbezkQI%252BsgbJ%252BQuAD0UPA%3D%3D) | 4 | 3
18 | J2 | 1 | Molex_PicoBlade_53261-0471_1x04-1MP_P1.25mm_Horizontal | Conn_01x04_Pin | Molex PicoBlade, 4 Pin, horizontal, mouser (https://cz.mouser.com/ProductDetail/Molex/53261-0471?qs=%252B72YyncTwW9e3et3PwnEMw%3D%3D) | 4 | 1
19 | J5,J4,J6 | 3 | Molex_PicoBlade_53398-0671_1x06-1MP_P1.25mm_Vertical | Conn_01x06_Pin | Molex PicoBlade, 6 Pin, vertical, mouser (https://cz.mouser.com/ProductDetail/Molex/53398-4006?qs=iLbezkQI%252BsgN7NG7c%2FlBfQ%3D%3D) | 7 | 3
20 | J3 | 1 | USB_Type_C | TYPE-C-31-M-12 | USB C mouser (https://cz.mouser.com/ProductDetail/GCT/USB4105-GF-A-060?qs=QNEnbhJQKvY2mocwNJzgfA%3D%3D&mgh=1) | 6 | 1
21 | U5 | 1 | TO-263-3_TabPin2 | LM1084-3.3 | LM1084IS-3.3-NOPB, mouser (https://cz.mouser.com/ProductDetail/Texas-Instruments/LM1084IS-3.3-NOPB?qs=X1J7HmVL2ZFUeOCa1Tl3Aw%3D%3D) | 3 | 1
22 | U4 | 1 | TO-263-3_TabPin2 | LM1084-5.0 | LM1084IS-5.0-NOPB, mouser (https://cz.mouser.com/ProductDetail/Texas-Instruments/LM1084IS-5.0-NOPB?qs=X1J7HmVL2ZHfHNZJcHduDA%3D%3D) | 3 | 1
23 | U2 | 1 | TSOT-23-6_HandSoldering | USBLC6-2SC6 | ESD protekce mouser (https://cz.mouser.com/ProductDetail/STMicroelectronics/USBLC6-2SC6?qs=po45yt2pPpu%2FhNIlwQdTlg%3D%3D) | 8 | 1
24 | U1 | 1 | ESP32-S3-WROOM-1 | ESP32-S3-WROOM-1 | ESP32 S3 WROOM1 mouser (https://cz.mouser.com/ProductDetail/Espressif-Systems/ESP32-S3-WROOM-1-N4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) | 3 | 1
25 | U3 | 1 | TSOP | TSOP382xx | TSOP382. 38kHz mouser (https://cz.mouser.com/ProductDetail/Vishay-Semiconductors/TSOP38238?qs=RzxYCzJDjPVjpHVZS582Ng%3D%3D) |  | 1
26 | J11 | 1 | AMASS_XT30PW-M | XT30PW-M | XT30PW, horizontal, TME (https://www.tme.eu/en/details/xt30pw-m/dc-power-connectors/amass/) | 5 | 1
27 | IC1,IC2 | 2 | DRV8874 | DRV8874PWPR | DRV8874. mouser (https://cz.mouser.com/ProductDetail/Texas-Instruments/DRV8874PWPR?qs=mAH9sUMRCtvh%2FSU15ywmDA%3D%3D) | 5 | 2
28 | SW1,SW4,SW3 | 3 | SW_SPST_B3U-1000P | SW_Push | B3U-1000P mouser (https://cz.mouser.com/ProductDetail/Omron-Electronics/B3U-1000P?qs=AO7BQMcsEu4ip80xyf2FwA%3D%3D) | 12 | 3
29 | SW2 | 1 | Custom_SPDT_4.8mm_Switch | SW_DPDT_x2 | SPDT Switch, mouser (https://cz.mouser.com/ProductDetail/E-Switch/500SSP3S2M2QEA) |  | 1
30 | H1,H3,H2 - H1, H2 | 5 | MountingHole_3.2mm_M3_Pad | MountingHole_Pad |  |  | 5
31 | U2,U1 | 3 | OnSemi_CASE100AQ - QRE1113 | QRE1113 | QRE1113 THT mouser (https://cz.mouser.com/ProductDetail/onsemi-Fairchild/QRE1113?qs=ne66E0WZ%2FFkJiYCW1J5zEw%3D%3D) | 15 + 4 pujceno + 10 doma | 3
 |  | 2 | CONNECTOR 1x3 | Sharp GP2Y0D810Z0F | SHARP Digital, Side senzor, Botland (https://botland.cz/digitalni-snimace-vzdalenosti/1623-sharp-gp2y0d810z0f-digitalni-snimac-vzdalenosti-10-cm-se-zasuvkou-na-pcb-pololu-1134-5904422305932.html) |  | 2
 |  | 71

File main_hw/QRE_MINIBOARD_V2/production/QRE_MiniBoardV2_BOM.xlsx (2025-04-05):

Designator | Footprint | Quantity | Value | Link
J1 | Molex_PicoBlade_53261-0471_1x04-1MP_P1.25mm_Horizontal | 1 | Conn_01x04_Pin | Molex PicoBlade, 4 Pin, horizontal, mouser
R1, R2 | 0805 | 2 | 10k
R3, R4 | 0805 | 2 | 100R
U1, U2 | OnSemi_CASE100CY | 2 | QRE1113 | QRE1113GR (https://cz.mouser.com/ProductDetail/onsemi-Fairchild/QRE1113GR?qs=Qb0BA3xILekkPpSVC5x7uQ%3D%3D)

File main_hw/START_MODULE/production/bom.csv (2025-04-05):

Designator | Footprint | Quantity | Value | Link
C1 | CP_EIA-3216-18_Kemet-A_Pad1.58x1.35mm_HandSolder | 1 | 10uF
C2 | 0805 | 1 | 100nF
D1, D2 | 0805 | 2 | LED
R1, R3 | 0805 | 2 | 220R
R2 | 0805 | 1 | 10k
J1 | PinHeader_1x03_P2.54mm_Vertical | 1 | Conn_01x03_Pin
J2 | PinHeader_1x04_P2.54mm_Vertical | 1 | Conn_01x04_Pin
SW1 | SW_SPST_EVQPE1 | 1 | SW_Push
U1 | SOIC-8W_5.3x5.3mm_P1.27mm | 1 | ATtiny85-20S
U2 | Vishay_MINICAST-3Pin | 1 | TSOP382xx

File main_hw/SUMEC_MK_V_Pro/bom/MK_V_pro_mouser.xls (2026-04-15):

Mfr Part Number (Input) | Manufacturer Part Number | Mouser Part Number | Manufacturer Name | Description | Quantity 1 | Unit Price 1 | Quantity 2 | Unit Price 2 | Quantity 3 | Unit Price 3 | Quantity 4 | Unit Price 4 | Quantity 5 | Unit Price 5 | Order Quantity | Order Unit Price | Min./Mult. | Availability | Lead Time in Days | Lifecycle | NCNR | RoHS | Pb Free | Package Type | Datasheet URL | Product Image | Design Risk
 |  | 815-AOTB252010S2R2MT |  |  | 10
 |  | 538-53398-4003 |  |  | 10
 |  | 538-53398-4004 |  |  | 10
 |  | 71-CRCW08051K00FKTC |  |  | 10
 |  | 511-USBLC6-2SC6 |  |  | 10
 |  | 595-DRV8874PWPR |  |  | 4
 |  | 490-CPT-1625-80SMTTR |  |  | 4

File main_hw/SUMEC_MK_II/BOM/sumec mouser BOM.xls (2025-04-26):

Mfr Part Number (Input) | Manufacturer Part Number | Mouser Part Number | Manufacturer Name | Description | Quantity 1 | Unit Price 1 | Quantity 2 | Unit Price 2 | Quantity 3 | Unit Price 3 | Quantity 4 | Unit Price 4 | Quantity 5 | Unit Price 5 | Order Quantity | Order Unit Price | Min./Mult. | Availability | Lead Time in Days | Lifecycle | NCNR | RoHS | Pb Free | Package Type | Datasheet URL | Product Image | Design Risk
 |  | 581-TCJA106M025R150E |  |  | 10
 |  | 80-T491A105K016 |  |  | 10
 |  | 581-KAF31GR71C106KU |  |  | 20
 |  | 581-12063C104JAT2A |  |  | 20
 |  | 652-CD1206-B260 |  |  | 10
 |  | 640-USB4105-GF-A-060 |  |  | 5
 |  | 71-CRCW12060000ZSTC |  |  | 20
 |  | 653-B3U-1000P |  |  | 10
 |  | 757-TB6612FNGC8EL |  |  | 10
 |  | 511-USBLC6-2SC6 |  |  | 10
 |  | 512-QRE1113 |  |  | 20
 |  | 513-NJM7805SDL1-TE1 |  |  | 10
 |  | 511-LD29150DT33R |  |  | 10
 |  | 603-AC1206JR-0715RL |  |  | 10
 |  | 667-ERA-8VRB1002V |  |  | 10
 |  | 603-RT1206BRD07100RL |  |  | 10

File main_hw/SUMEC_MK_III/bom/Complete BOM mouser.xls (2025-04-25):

Mfr Part Number (Input) | Manufacturer Part Number | Mouser Part Number | Manufacturer Name | Description | Quantity 1 | Unit Price 1 | Quantity 2 | Unit Price 2 | Quantity 3 | Unit Price 3 | Quantity 4 | Unit Price 4 | Quantity 5 | Unit Price 5 | Order Quantity | Order Unit Price | Min./Mult. | Availability | Lead Time in Days | Lifecycle | NCNR | RoHS | Pb Free | Package Type | Datasheet URL | Product Image | Design Risk
 |  | 652-CHP0805AFX-5600L |  |  | 10
 |  | 667-ERJ-6RED15R0V |  |  | 10
 |  | 71-RCC080510K0FKEA |  |  | 10
 |  | 71-CRCW0805100RFKEAH |  |  | 10
 |  | 581-08055C223KAT4A |  |  | 10
 |  | 603-AC805KRX7R7BB104 |  |  | 25
 |  | 80-T491A106K016 |  |  | 25
 |  | 327-VFHV1112H3BZ2BTR |  |  | 5
 |  | 327-FY1112HTR |  |  | 5
 |  | 327-VFHD1112H3B72BTR |  |  | 5
 |  | 538-53398-4004 |  |  | 3
 |  | 538-53398-4003 |  |  | 6
 |  | 538-53261-0471 |  |  | 3
 |  | 538-53398-4006 |  |  | 6
 |  | 640-USB4105-GF-A-060 |  |  | 5
 |  | 926-LM1084IS-3.3NOPB |  |  | 3
 |  | 926-LM1084IS50NOPB |  |  | 3
 |  | 356-ESP32-S3WROOM1N4 |  |  | 3
 |  | 595-DRV8874PWPR |  |  | 5
 |  | 653-B3U-1000P |  |  | 10
 |  | 612-500SSP3S2M2QEA |  |  | 3

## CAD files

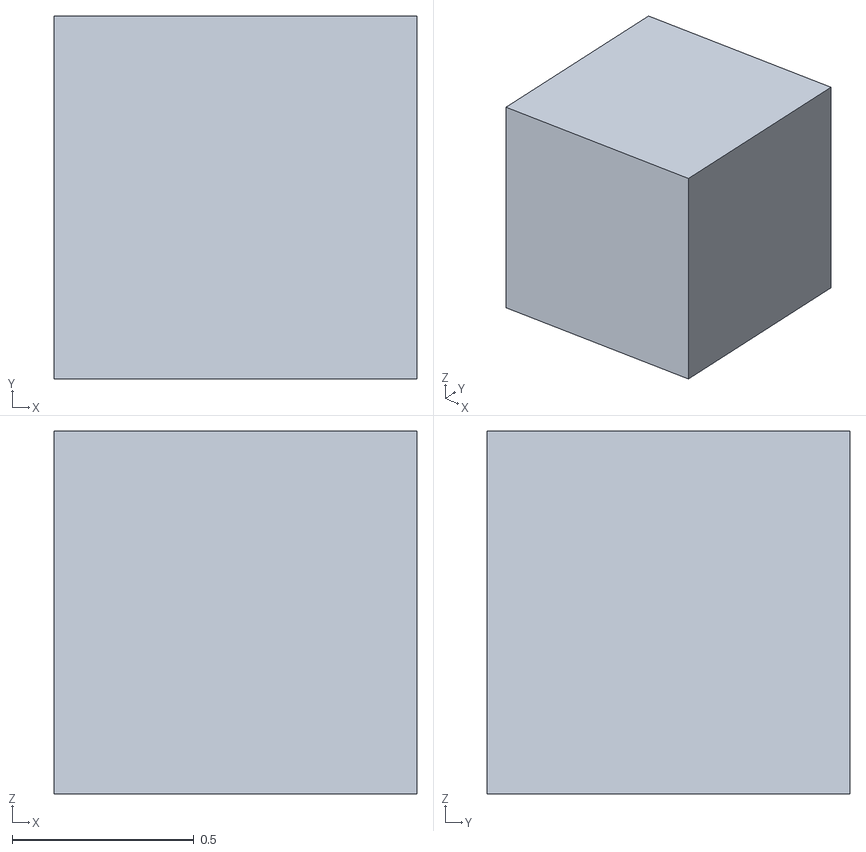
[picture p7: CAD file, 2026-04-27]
main_hw/IMU_vis/Python_IMU_vis/cube.obj
1.00 x 1.00 x 1.00

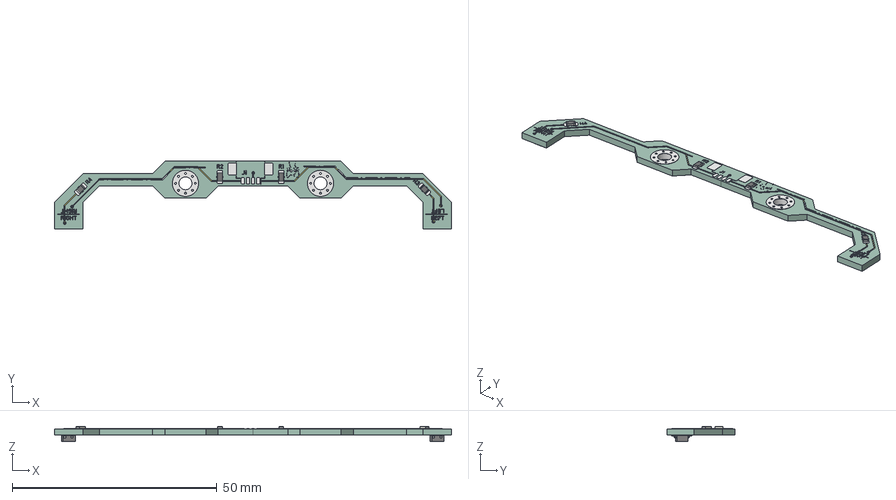
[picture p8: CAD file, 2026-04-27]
main_hw/QRE_MINIBOARD_V2/QRE_MiniBoard-V2.step
97.0 x 16.5 x 3.58 mm
R_0805_2012Metric x 4
OnSemi_CASE100CY x 2
QRE_MiniBoardV2_copper
QRE_MiniBoardV2_pad
QRE_MiniBoardV2_via
QRE_MiniBoardV2_silkscreen x 2
QRE_MiniBoardV2_PCB

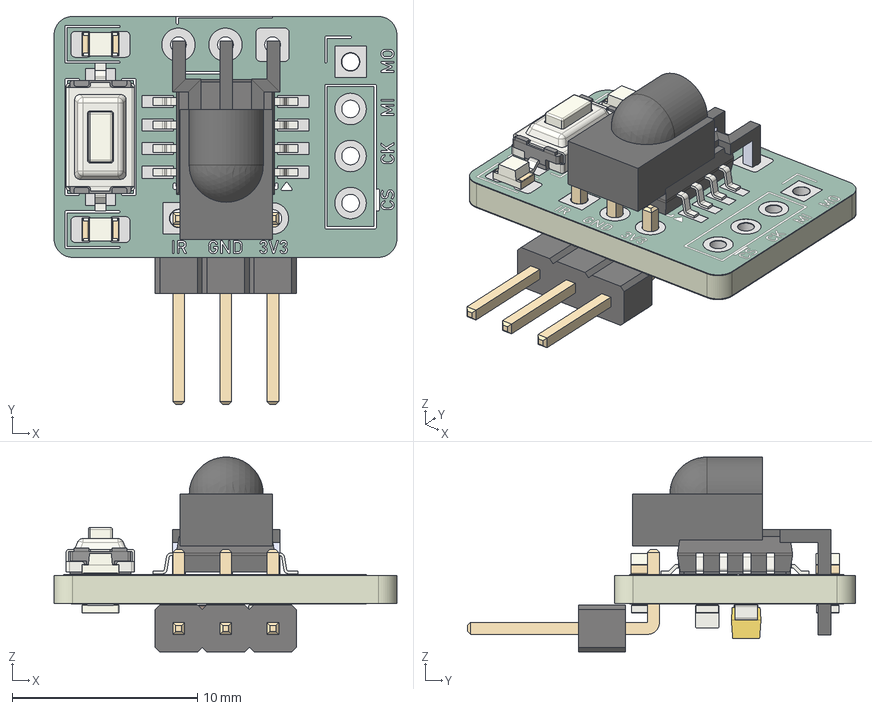
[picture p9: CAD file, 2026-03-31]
main_hw/START_MODULE/START_MODULE.step
18.5 x 20.9 x 10.5 mm
SW_Tactile_SPST_NO_Straight_CK_PTS636Sx25SMTRLFS
LED_0805_2012Metric x 2
SOIC-8_5.3x6.2mm_P1.27mm
R_0805_2012Metric x 3
CP_EIA-3216-18_Kemet-A
C_0805_2012Metric
PinHeader_1x03_P2.54mm_Horizontal
START_MODULE_copper
START_MODULE_pad
START_MODULE_via
START_MODULE_silkscreen x 2
START_MODULE_soldermask x 2
START_MODULE_PCB

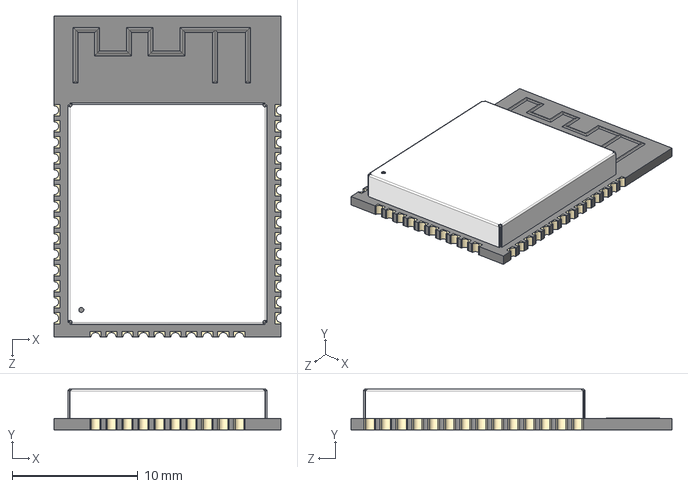
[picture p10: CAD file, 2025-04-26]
main_hw/SUMEC_MK_I/KiCAD FS/ESP32 (Microcontroler)/ESP32-WROOM-32D.step
18.0 x 3.25 x 25.5 mm

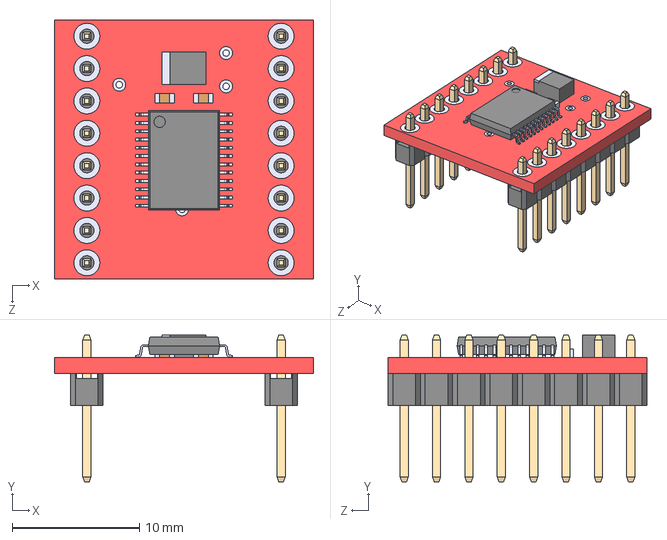
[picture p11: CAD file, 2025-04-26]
main_hw/SUMEC_MK_I/KiCAD FS/H-BRIDGE/ROB-14450.step
20.3 x 11.5 x 20.3 mm

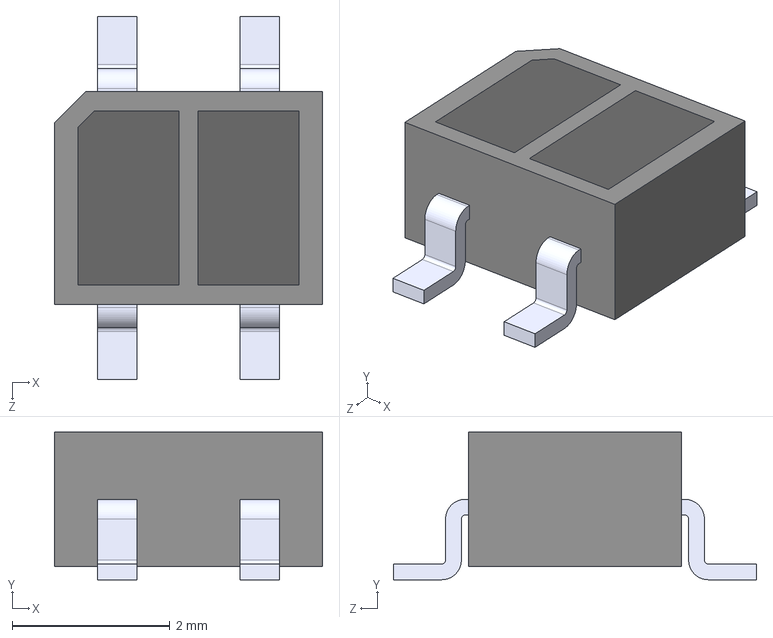
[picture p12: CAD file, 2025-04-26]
main_hw/SUMEC_MK_I/KiCAD FS/QRE1113GR (Line sensor)/QRE1113GR.step
3.40 x 1.87 x 4.60 mm

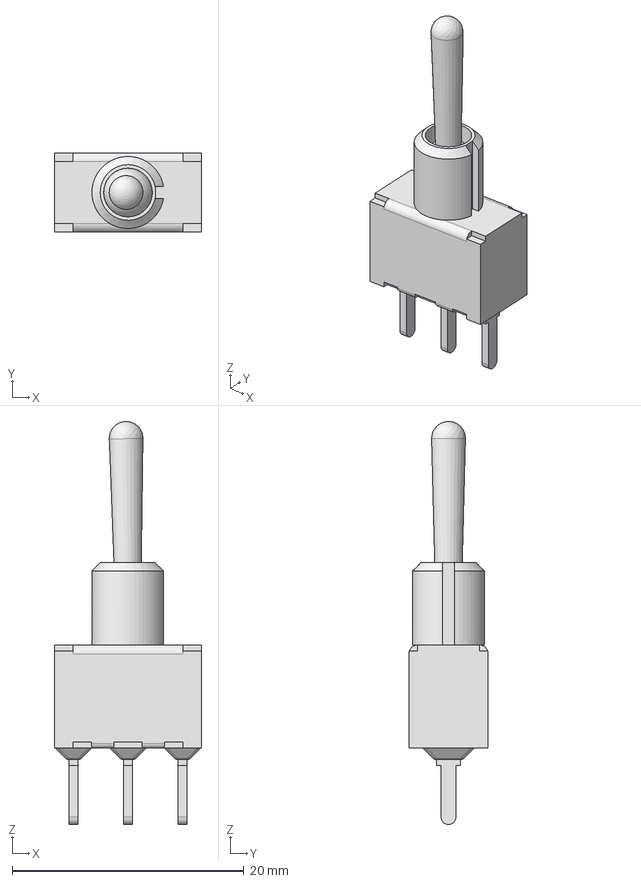
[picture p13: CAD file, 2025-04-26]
main_hw/SUMEC_MK_I/KiCAD FS/SWITCH SPDT/100SP1T1B4M2QE.step
12.7 x 6.86 x 34.8 mm

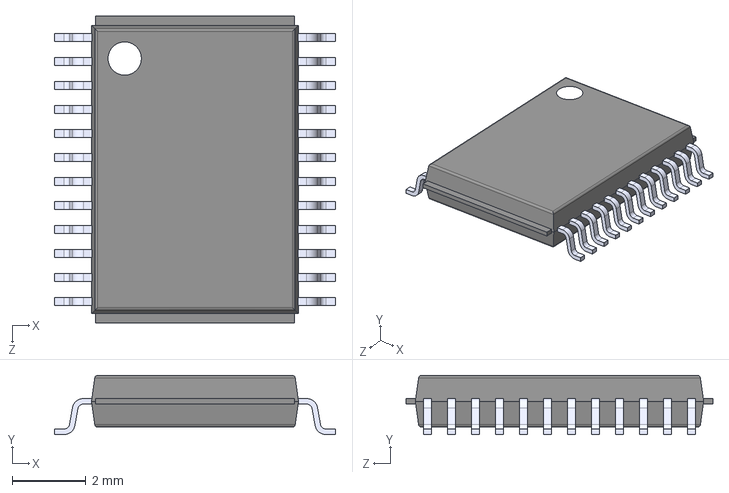
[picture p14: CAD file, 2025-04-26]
main_hw/SUMEC_MK_I/KiCAD FS/TB6612FNG (Motor driver)/TB6612FNG_C_8_EL.step
7.60 x 1.60 x 8.30 mm

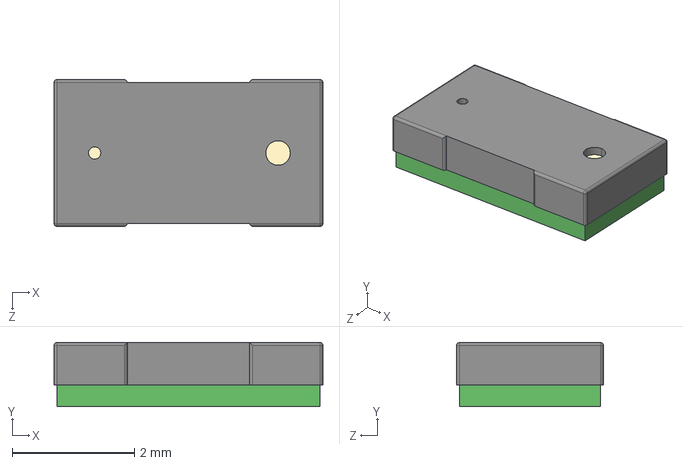
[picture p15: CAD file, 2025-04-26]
main_hw/SUMEC_MK_I/KiCAD FS/VL53L0X/VL53L0X.step
4.40 x 1.05 x 2.40 mm

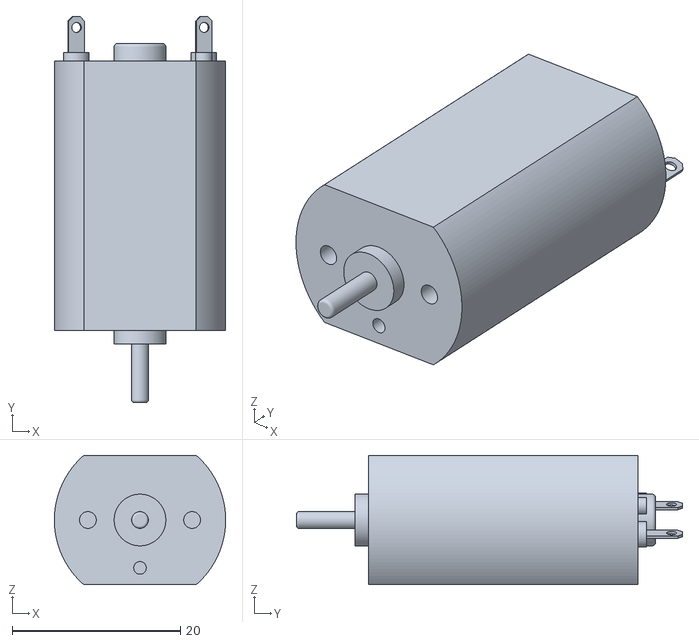
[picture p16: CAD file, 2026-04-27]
main_hw/IMU_vis/Python_IMU_vis/model.obj
20.4 x 46.0 x 15.4

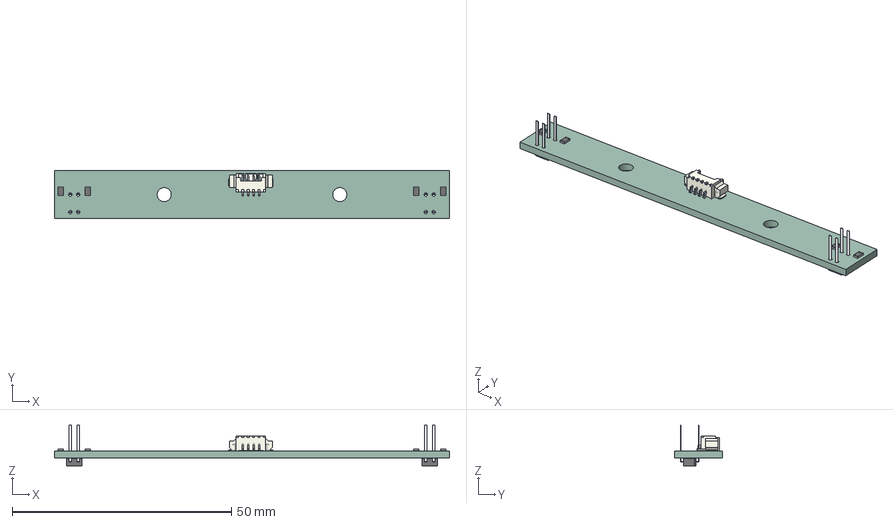
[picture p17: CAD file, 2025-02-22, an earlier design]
main_hw/QRE_MINIBOARD/MiniBoard_3d/QRE MiniBoards Board.step
90.0 x 11.0 x 9.25 mm
QRE MiniBoards PCB

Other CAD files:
main_hw/SUMEC_MK_III/sumec/COMPOUND.ipt
main_hw/SUMEC_MK_III/sumec/COMPOUND_1.ipt
main_hw/SUMEC_MK_III/sumec/COMPOUND_2.ipt
main_hw/SUMEC_MK_III/sumec/COMPOUND_3.ipt
main_hw/SUMEC_MK_III/sumec/COMPOUND_4.ipt
main_hw/SUMEC_MK_III/sumec/CP_EIA-3216-18_Kemet-A.iam
main_hw/SUMEC_MK_III/sumec/C_0805_2012Metric.iam
main_hw/SUMEC_MK_III/sumec/DRV8874.iam
main_hw/SUMEC_MK_III/sumec/D_1206_3216Metric.iam
main_hw/SUMEC_MK_III/sumec/ESP32-S3-WROOM-1.iam
main_hw/SUMEC_MK_III/sumec/JST_XH_B4B-XH-A_1x04_P2.50mm_Vertical.iam
main_hw/SUMEC_MK_III/sumec/LED_0805_2012Metric.iam
main_hw/SUMEC_MK_III/sumec/Molex_PicoBlade_53398-0371_1x03-1MP_P1.25mm_Vertical.iam
main_hw/SUMEC_MK_III/sumec/Molex_PicoBlade_53398-0471_1x04-1MP_P1.25mm_Vertical.iam
main_hw/SUMEC_MK_III/sumec/Molex_PicoBlade_53398-0671_1x06-1MP_P1.25mm_Vertical.iam
main_hw/SUMEC_MK_III/sumec/R_0805_2012Metric.iam
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

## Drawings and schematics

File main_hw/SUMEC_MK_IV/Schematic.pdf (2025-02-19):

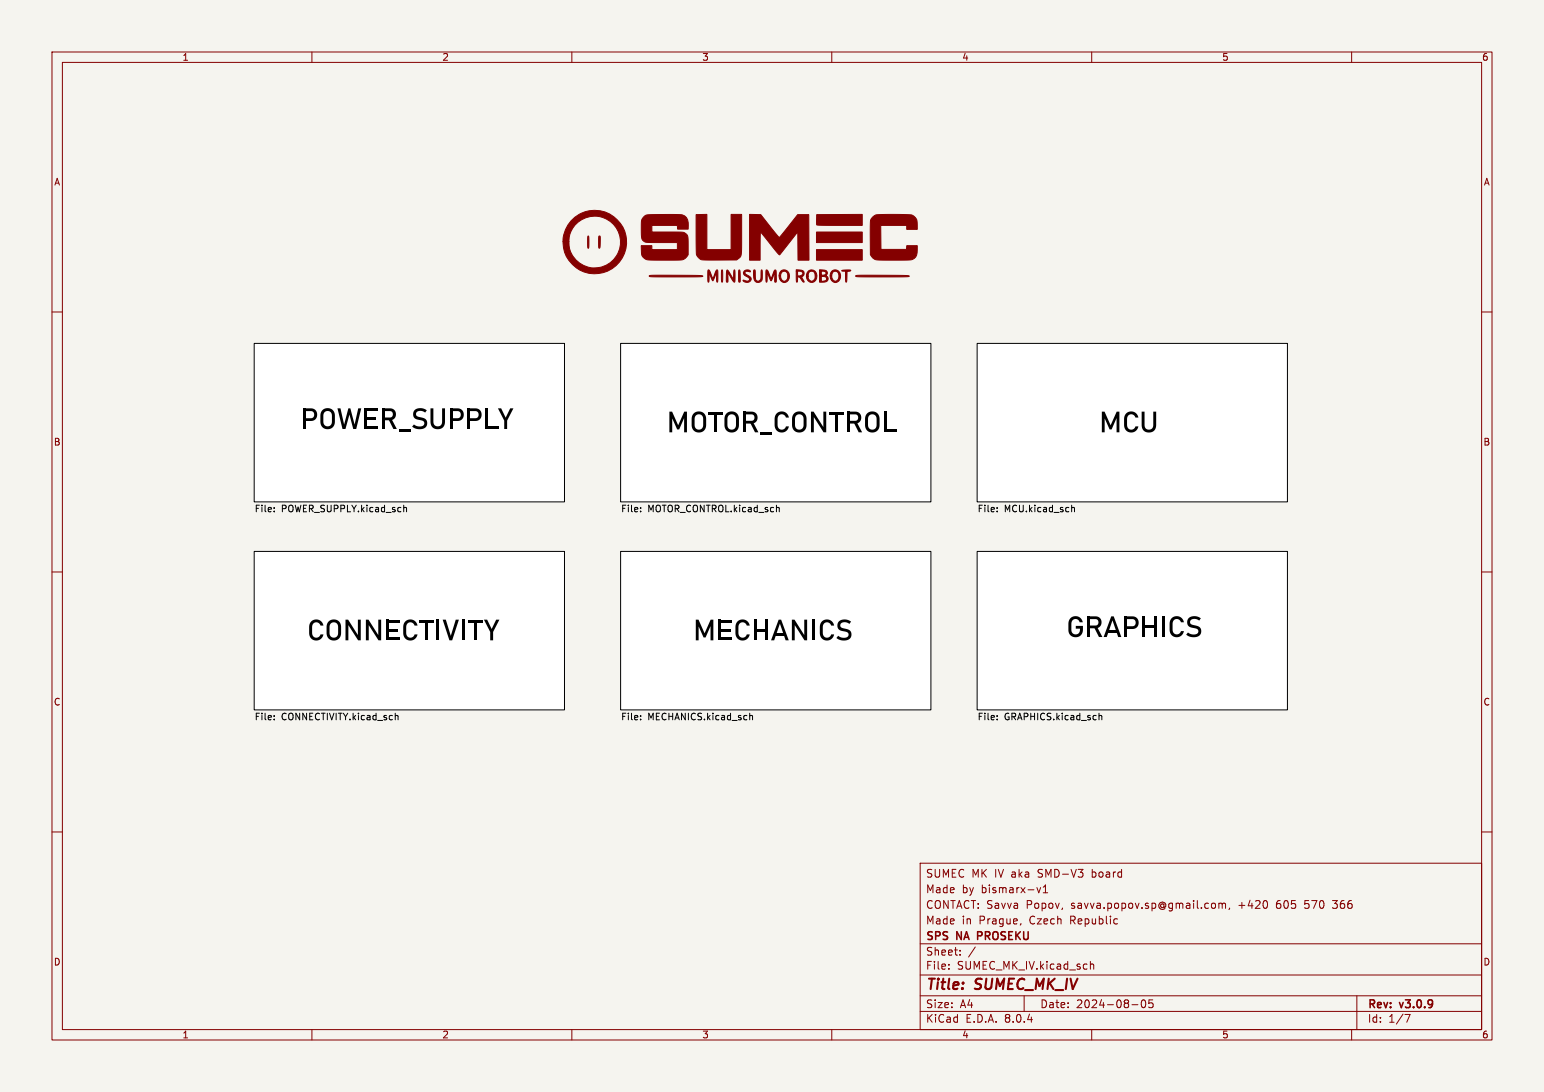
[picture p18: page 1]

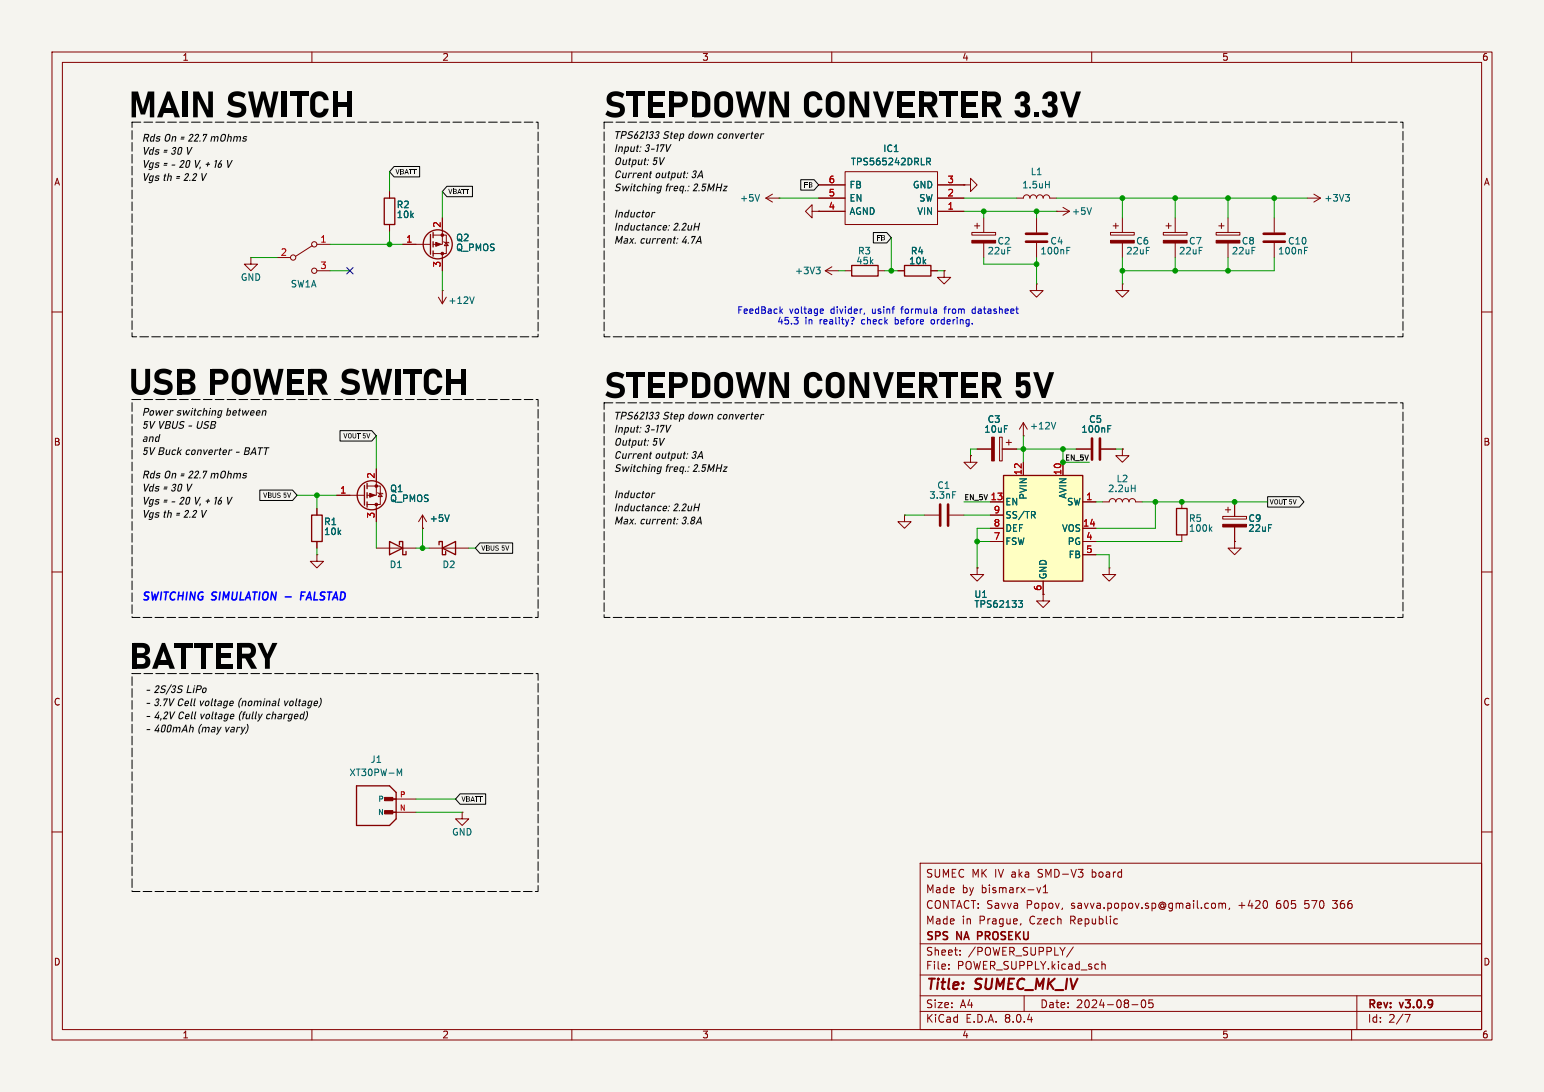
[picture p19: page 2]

Inductance: 2.2uH Max. current: 3.8A MAINSWITCH

Input: 3-17V Output: 5V Current output: 3A

6 FSW 7 DEF 8 SS/TR 9 U1 TPS62133 R4

6 FSW 7 DEF 8 SS/TR 9 R4

SWITCHING SIMULATION - FALSTAD (https://www.youtube.com/watch?v=lVDUcCuKls0) USBPOWERSWITCH Power switching between

TPS62133Step down converter

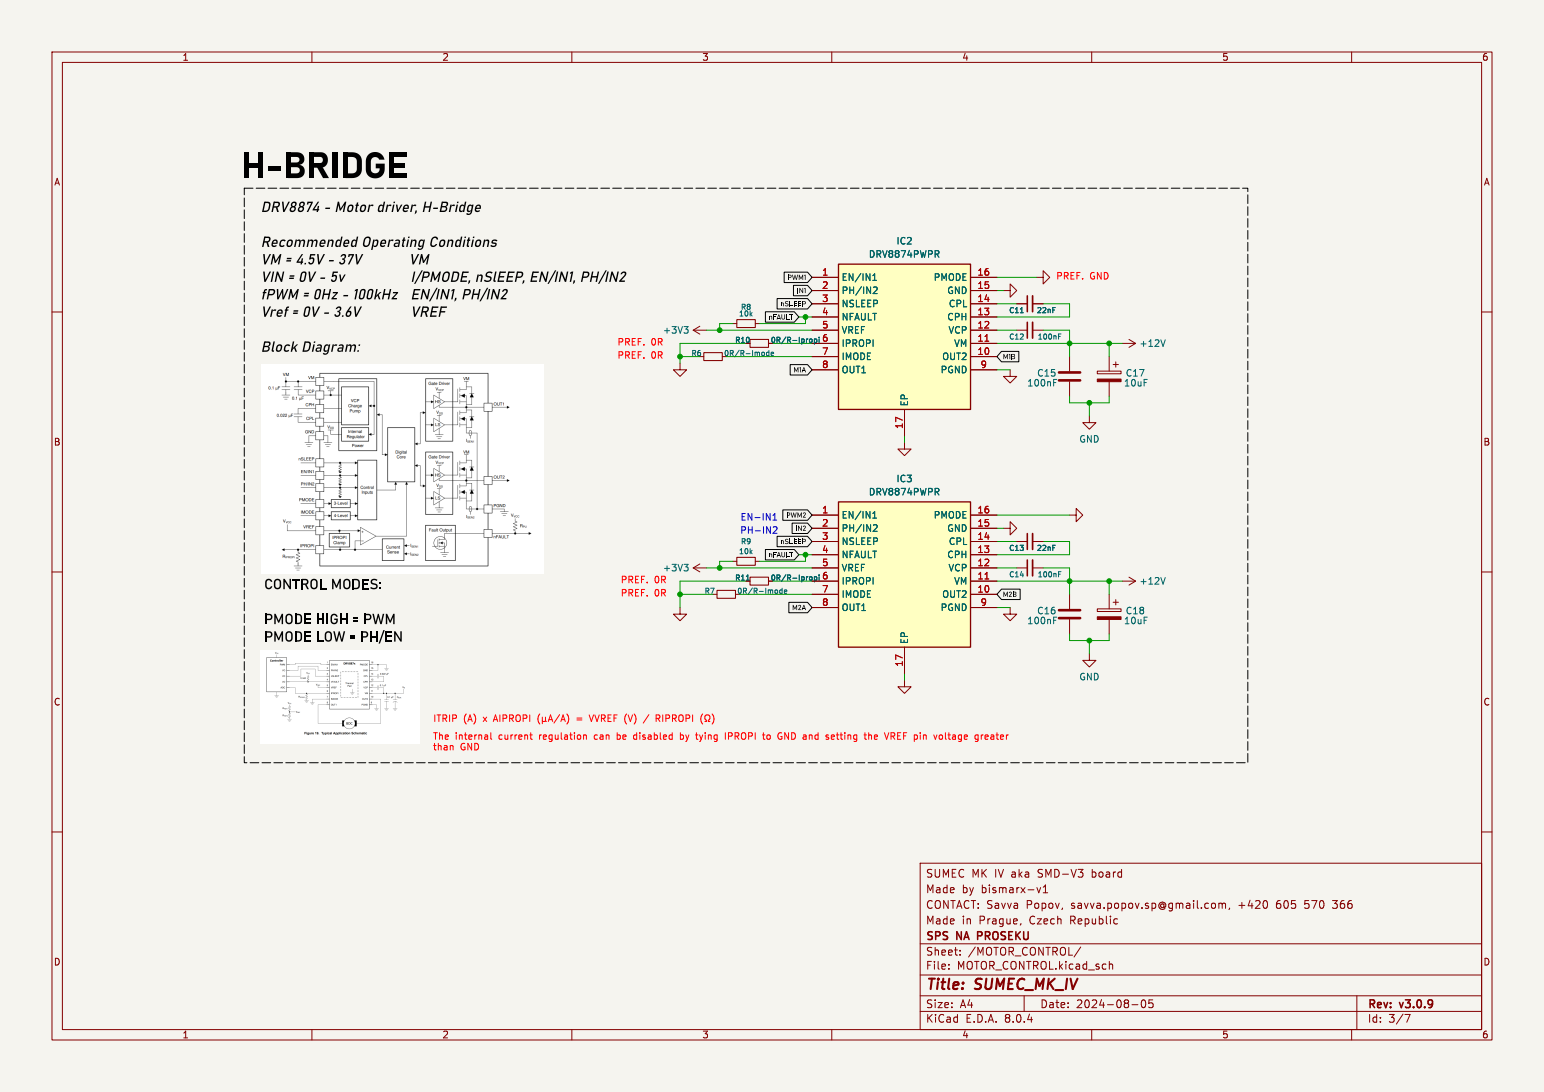
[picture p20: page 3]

ITRIP (A) x AIPROPI þÿ(¼A/A) = VVREF (V) / RIPROPI þÿ(!&)EN-IN1 CONTROLMODES:

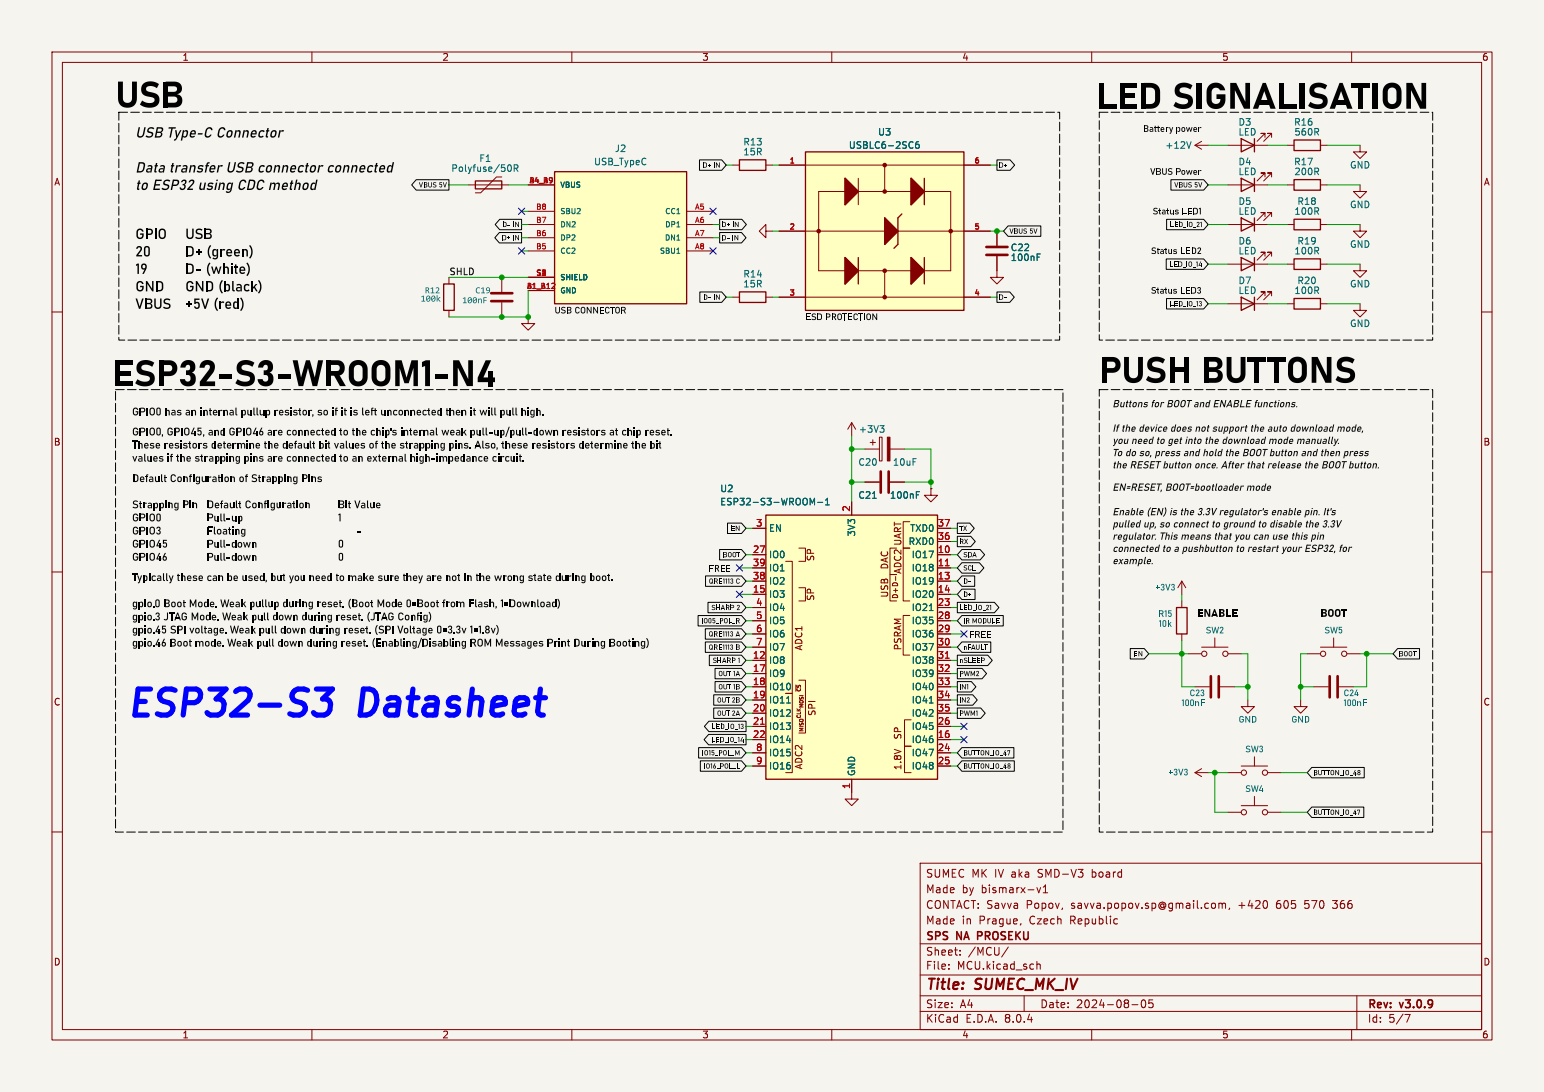
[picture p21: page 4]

Data transfer USBconnector connected
to ESP32using CDCmethod

VBUSPower EN=RESET,BOOT=bootloadermode Enable (EN) is the 3.3Vregulator's enable pin. It's pulled up, so connect to ground to disable the 3.3V

If the device does not support the auto download mode, you need to get into the download mode manually. Todo so, press and hold the BOOTbutton and then press

regulator. This means that you can use this pin
connected to a pushbutton to restart your ESP32,for example.

Typically these can be used, but you need to make sure they are not in the wrong state during boot. gpio.0Boot Mode.Weakpullup during reset. (Boot Mode 0=Boot from Flash, 1=Download)

gpio.3 JTAGMode.Weakpull down during reset. (JTAGConfig)
gpio.45 SPI voltage. Weakpull down during reset. (SPIVoltage 0=3.3v1=1.8v)

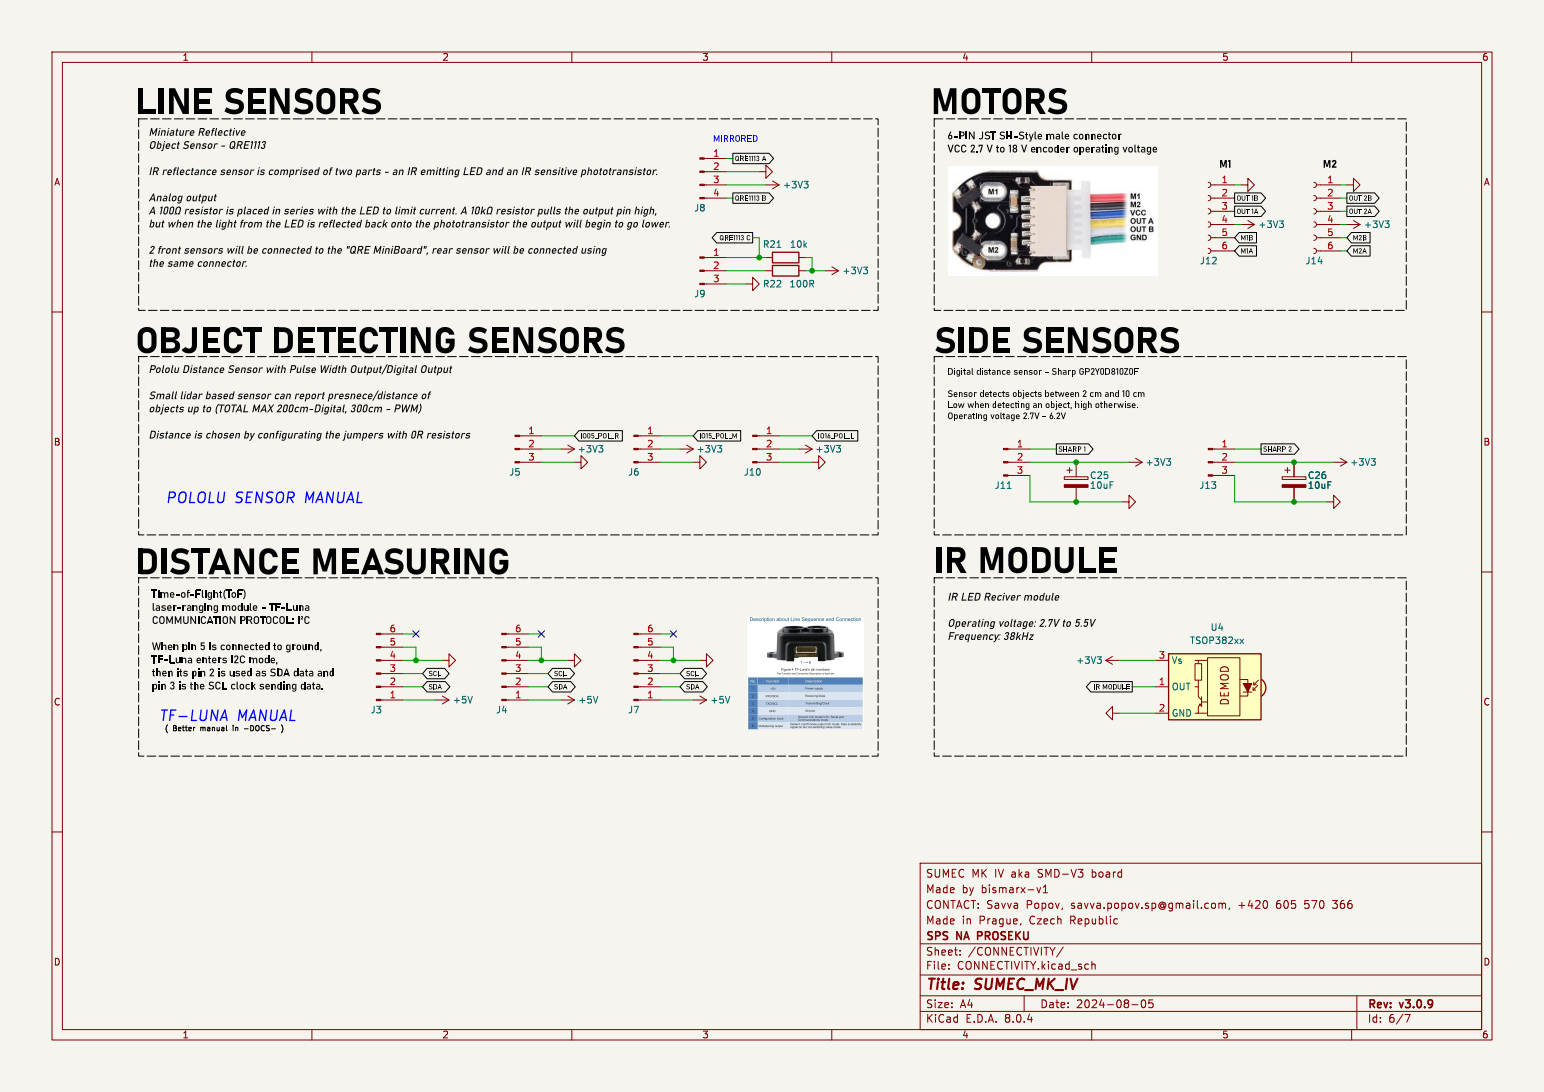
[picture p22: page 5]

pin 3 is the SCLclock sending data. Miniature Reflective Object Sensor - QRE1113

6-PIN JSTSH-Style male connector VCC2.7V to 18V encoder operating voltage

IR reflectance sensor is comprised of two parts - an IR emitting LED and an IR sensitive phototransistor.

the same connector. OBJECTDETECTINGSENSORS

Analog output A þÿ100© resistor is placed in series with the LED to limit current. A þÿ10k© resistor pulls the output pin high, but when the light from the LED is reflected back onto the phototransistor the output will begin to go lower. 2 front sensors will be connected to the "QREMiniBoard", rear sensor will be connected using

Pololu Distance Sensor with Pulse Width Output/Digital Output Small lidar based sensor can report presnece/distance of objects up to (TOTALMAX200cm-Digital, 300cm - PWM) Distance is chosen by configurating the jumpers with 0R resistors TF-LUNA MANUAL

Digital distance sensor - Sharp GP2Y0D810Z0F Sensor detects objects between 2 cm and 10cm

IR LED Reciver module Operating voltage: 2.7Vto 5.5V

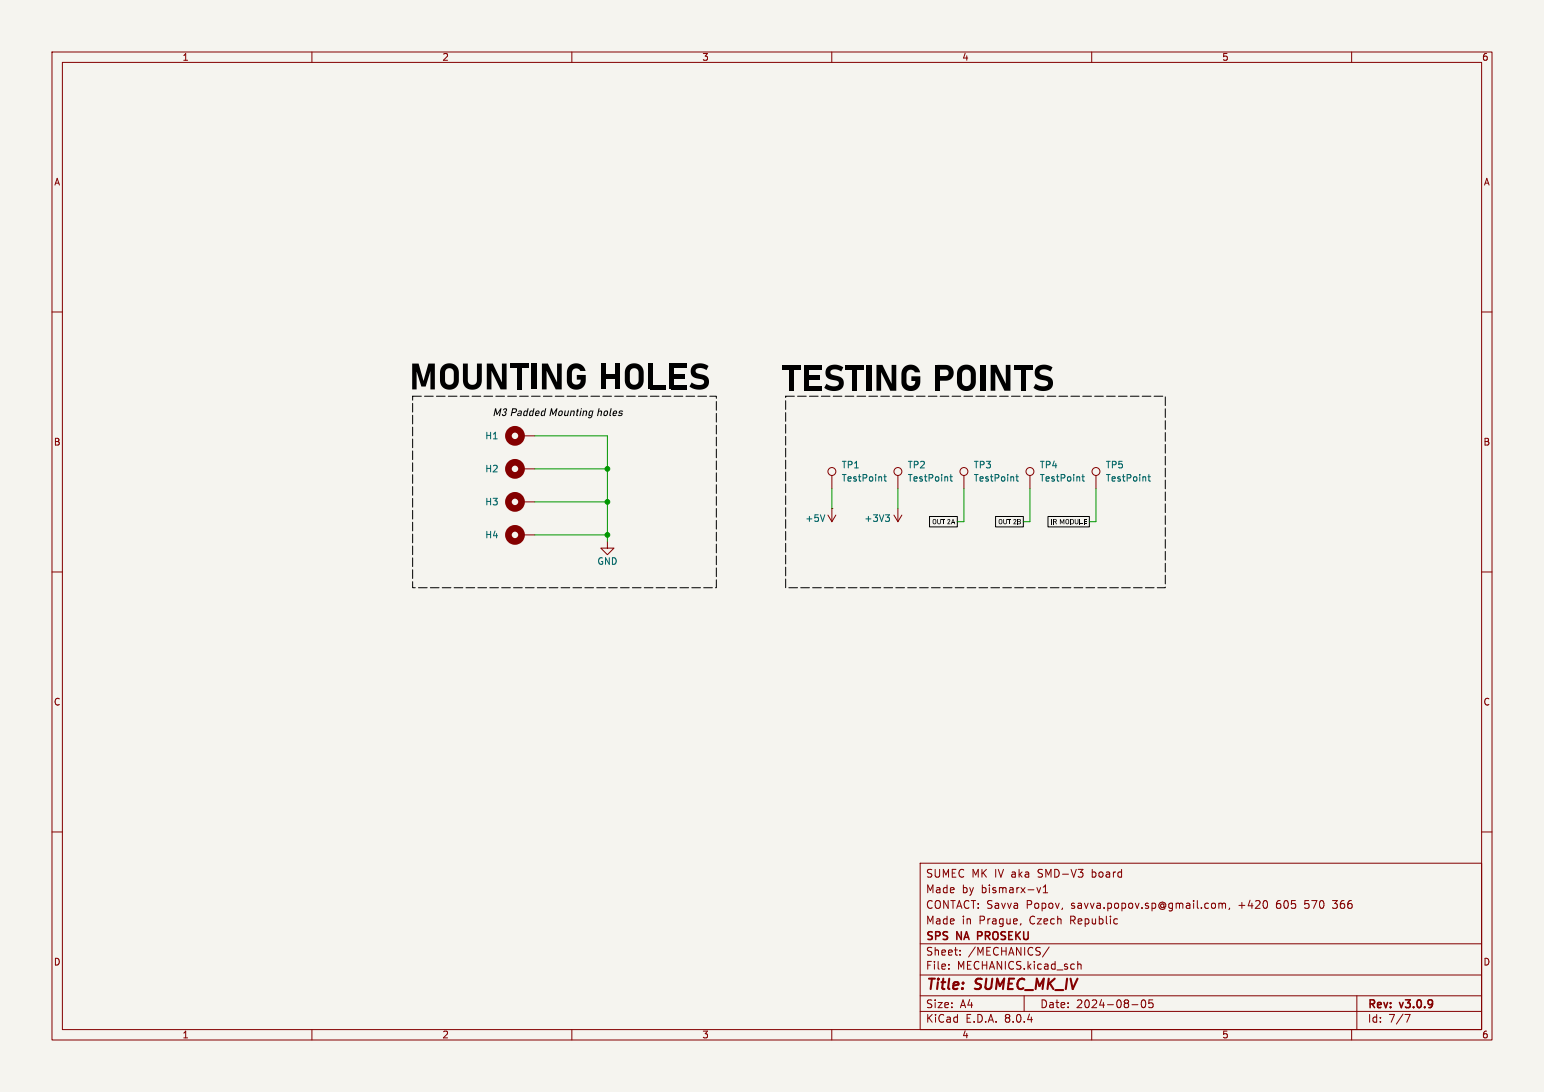
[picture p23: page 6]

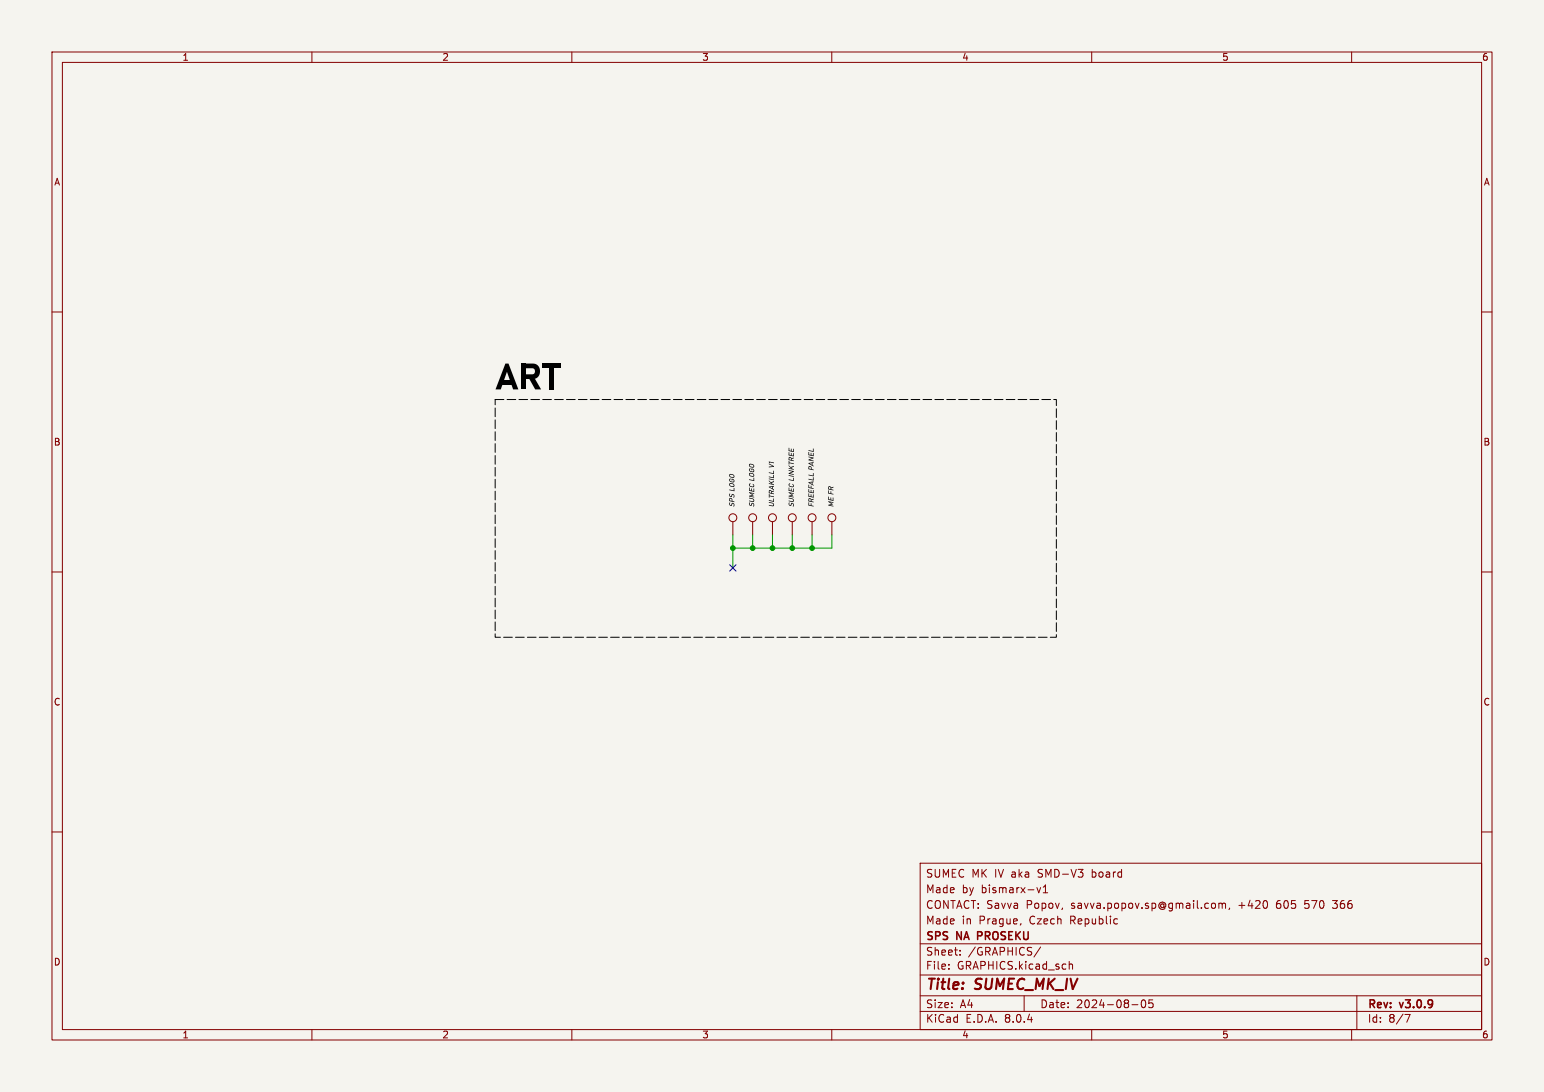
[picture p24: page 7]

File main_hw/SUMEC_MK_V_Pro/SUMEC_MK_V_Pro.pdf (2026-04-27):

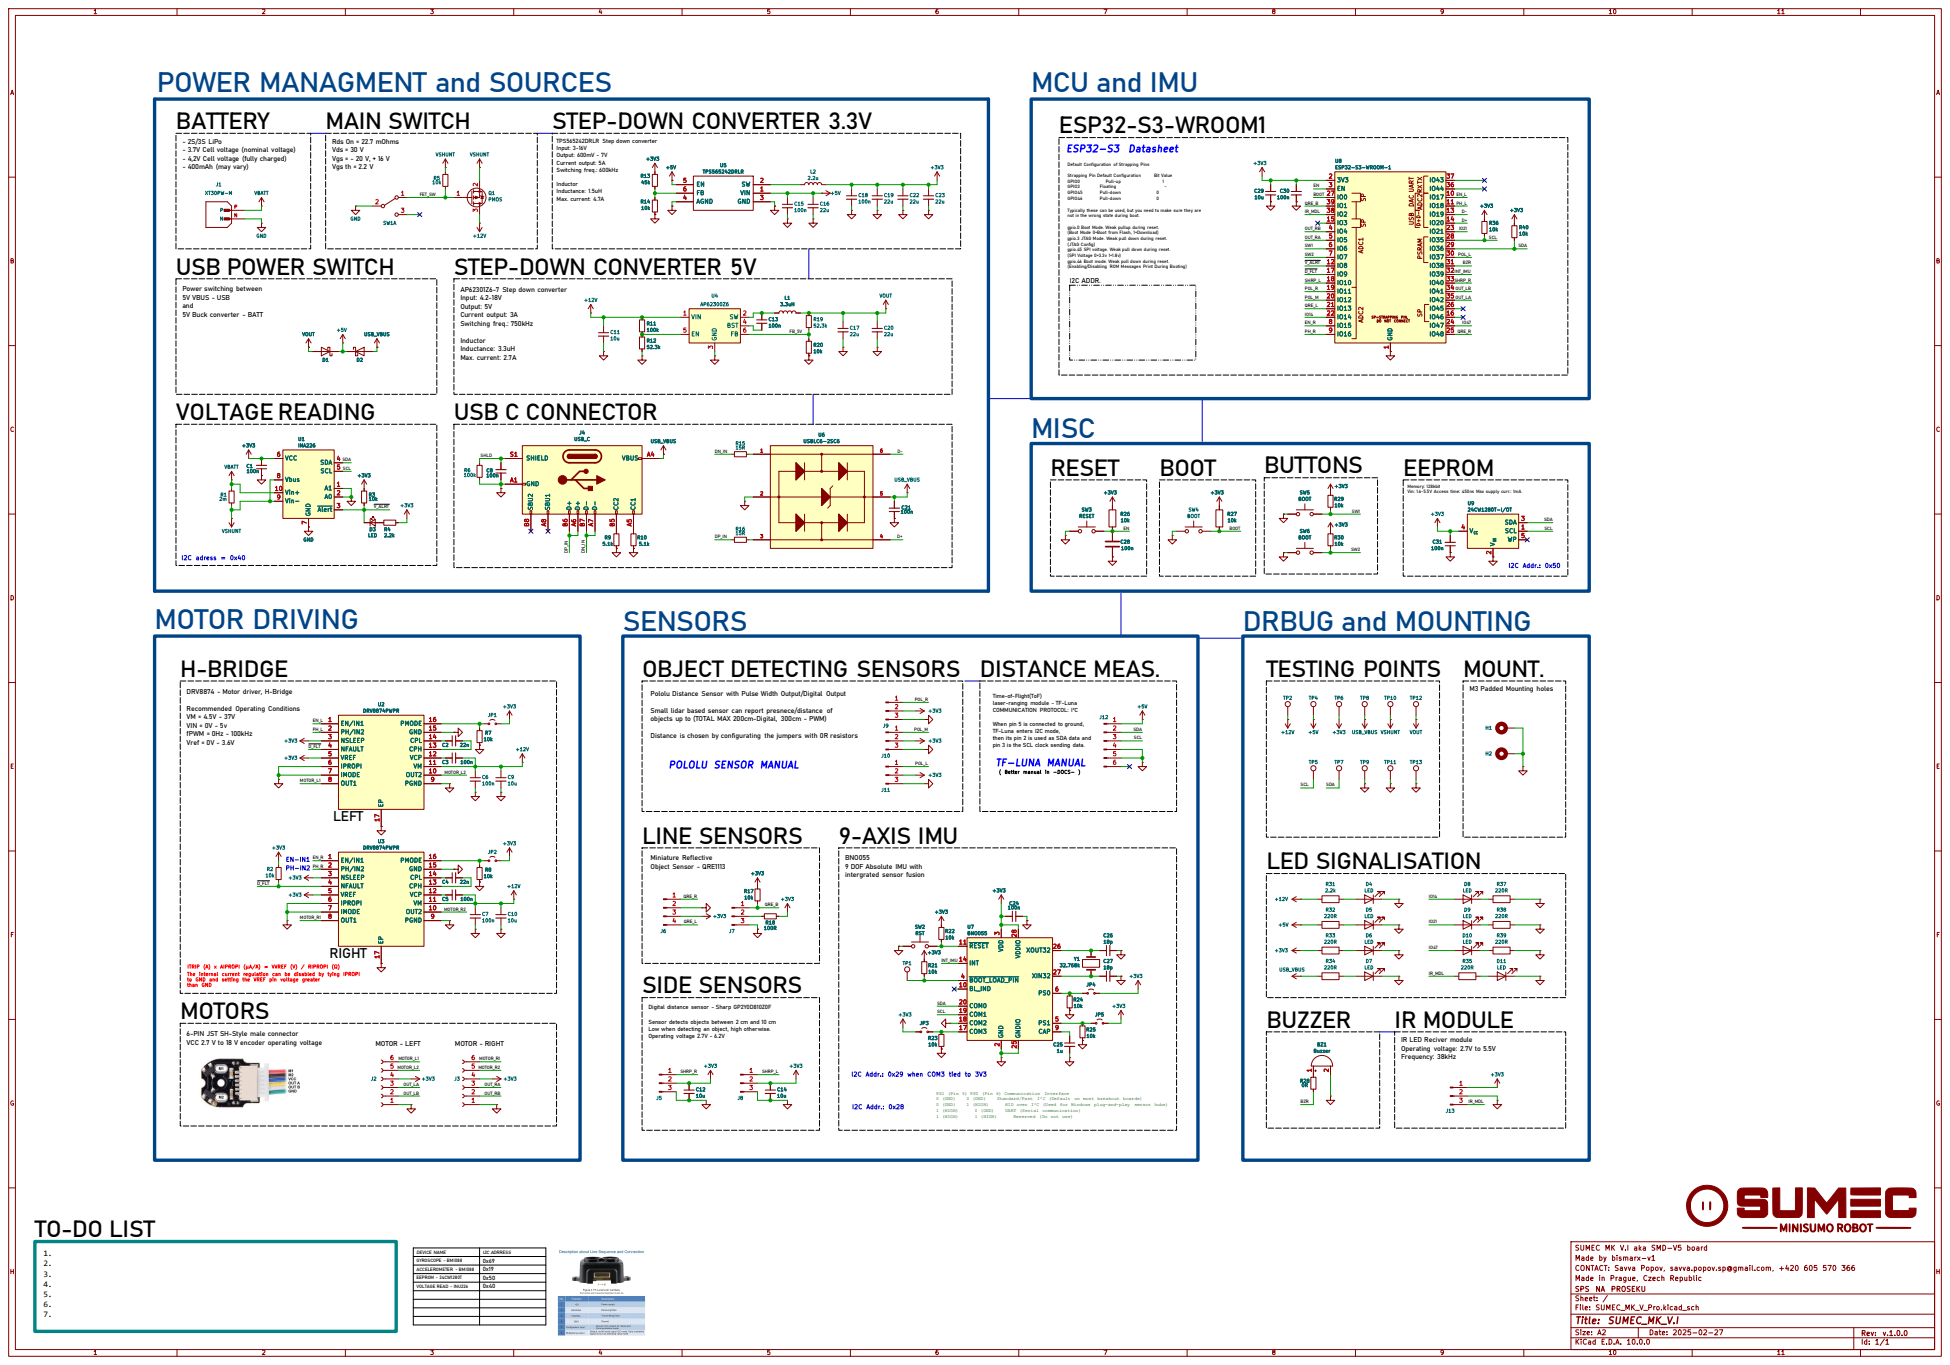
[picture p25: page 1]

ITRIP (A) x AIPROPI (μA/A) = VVREF (V) / RIPROPI (Ω) BATTERY

intergrated sensor fusion Pololu Distance Sensor with Pulse Width Output/Digital Output Small lidar based sensor can report presnece/distance of objects up to (TOTAL MAX 200cm-Digital, 300cm - PWM) Distance is chosen by configurating the jumpers with 0R resistors POWER MANAGMENT and SOURCES

- 2S/3S LiPo - 3.7V Cell voltage (nominal voltage) - 4,2V Cell voltage (fully charged) - 400mAh (may vary)

Rds On = 22.7 mOhms Vds = 30 V

TPS565242DRLR Step down converter
Input: 3-16V Output: 600mV - 7V Current output: 5A

AP62301Z6-7 Step down converter
Input: 4.2-18V Output: 5V Current output: 3A

Inductor Inductance: 3.3uH Max. current: 2.7A

M3 Padded Mounting holes MOUNT.

DRV8874 - Motor driver, H-Bridge Recommended Operating Conditions VM = 4.5V - 37V

Time-of-Flight(ToF)
laser-ranging module - TF-Luna COMMUNICATION PROTOCOL: I²C When pin 5 is connected to ground, TF-Luna enters I2C mode, then its pin 2 is used as SDA data and pin 3 is the SCL clock sending data.

BNO055
9 DOF Absolute IMU with

The internal current regulation can be disabled by tying IPROPI to GND and setting the VREF pin voltage greater

Low when detecting an object, high otherwise. Operating voltage 2.7V - 6.2V 6-PIN JST SH-Style male connector VCC 2.7 V to 18 V encoder operating voltage

IR LED Reciver module Operating voltage: 2.7V to 5.5V

I2C Addr.: 0x29 when COM3 tied to 3V3

PS1 (Pin 5) PS0 (Pin 6) Communication Interface

DEVICE NAME | I2C ADRRESS GYROSCOPE - BMI088 0x69

SUMEC MK V.I aka SMD-V5 board
CONTACT: Savva Popov, savva.popov.sp@gmail.com, +420 605 570 366 Made by bismarx-v1

ACCELEROMETER - BMI088 | 0x19
EEPROM - 24CW1280T | 0x50
VOLTAGE READ - INU226 | 0x40

SPS NA PROSEKU Made in Prague, Czech Republic

Size: A2 | Rev: v.1.0.0

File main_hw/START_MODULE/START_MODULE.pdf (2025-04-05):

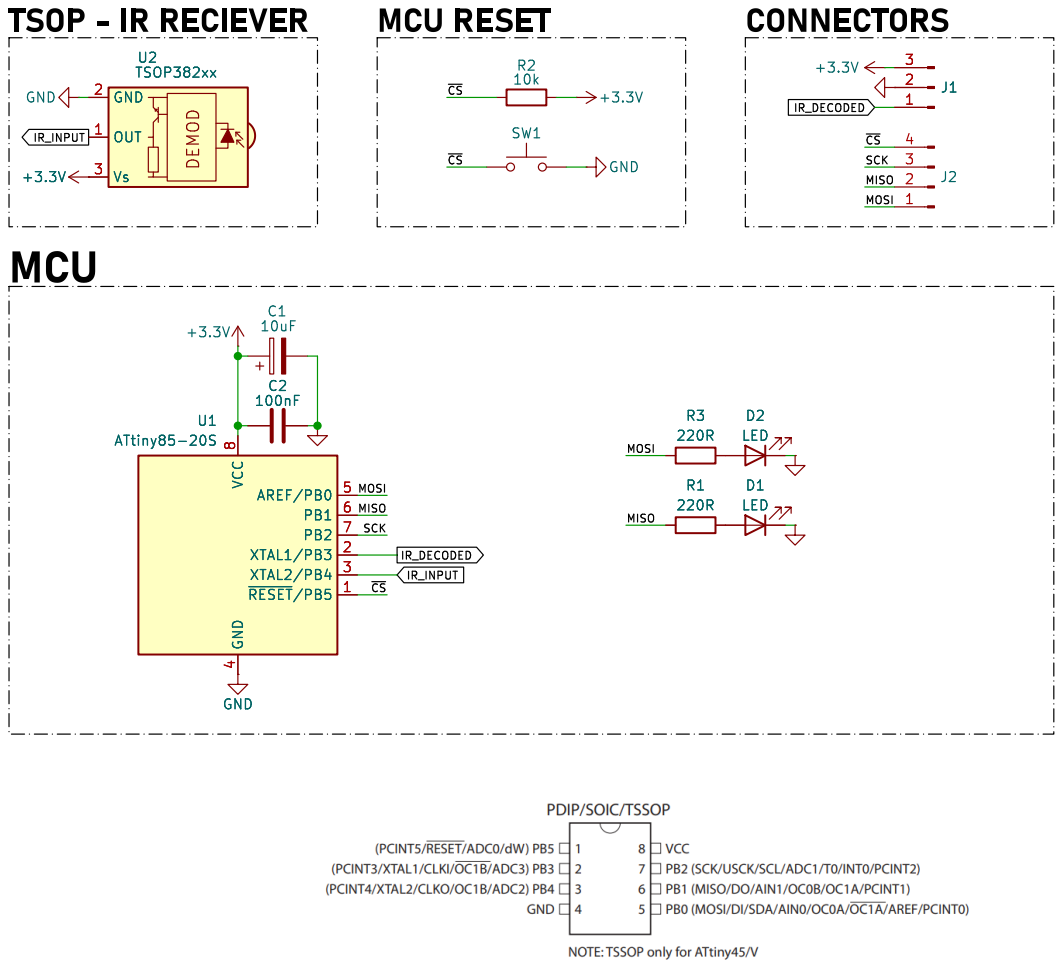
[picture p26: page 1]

8 GND
Id: 1/1 Title: File: START_MODULE.kicad_sch Sheet: / VCC

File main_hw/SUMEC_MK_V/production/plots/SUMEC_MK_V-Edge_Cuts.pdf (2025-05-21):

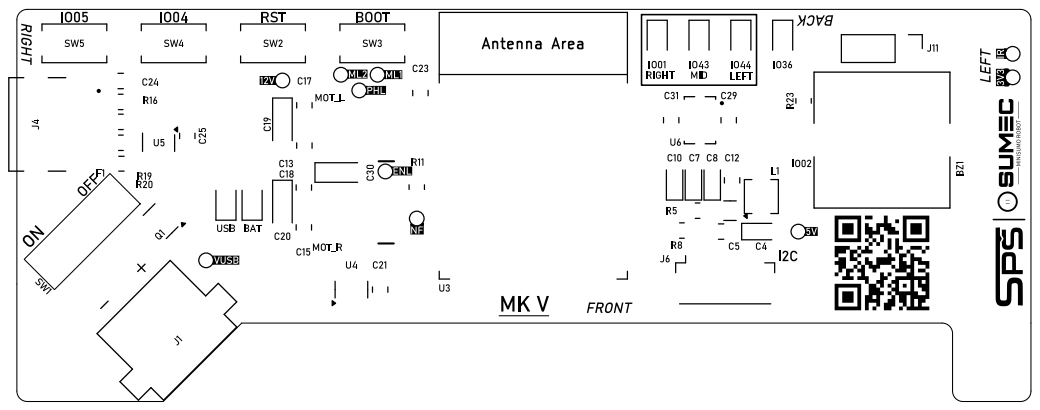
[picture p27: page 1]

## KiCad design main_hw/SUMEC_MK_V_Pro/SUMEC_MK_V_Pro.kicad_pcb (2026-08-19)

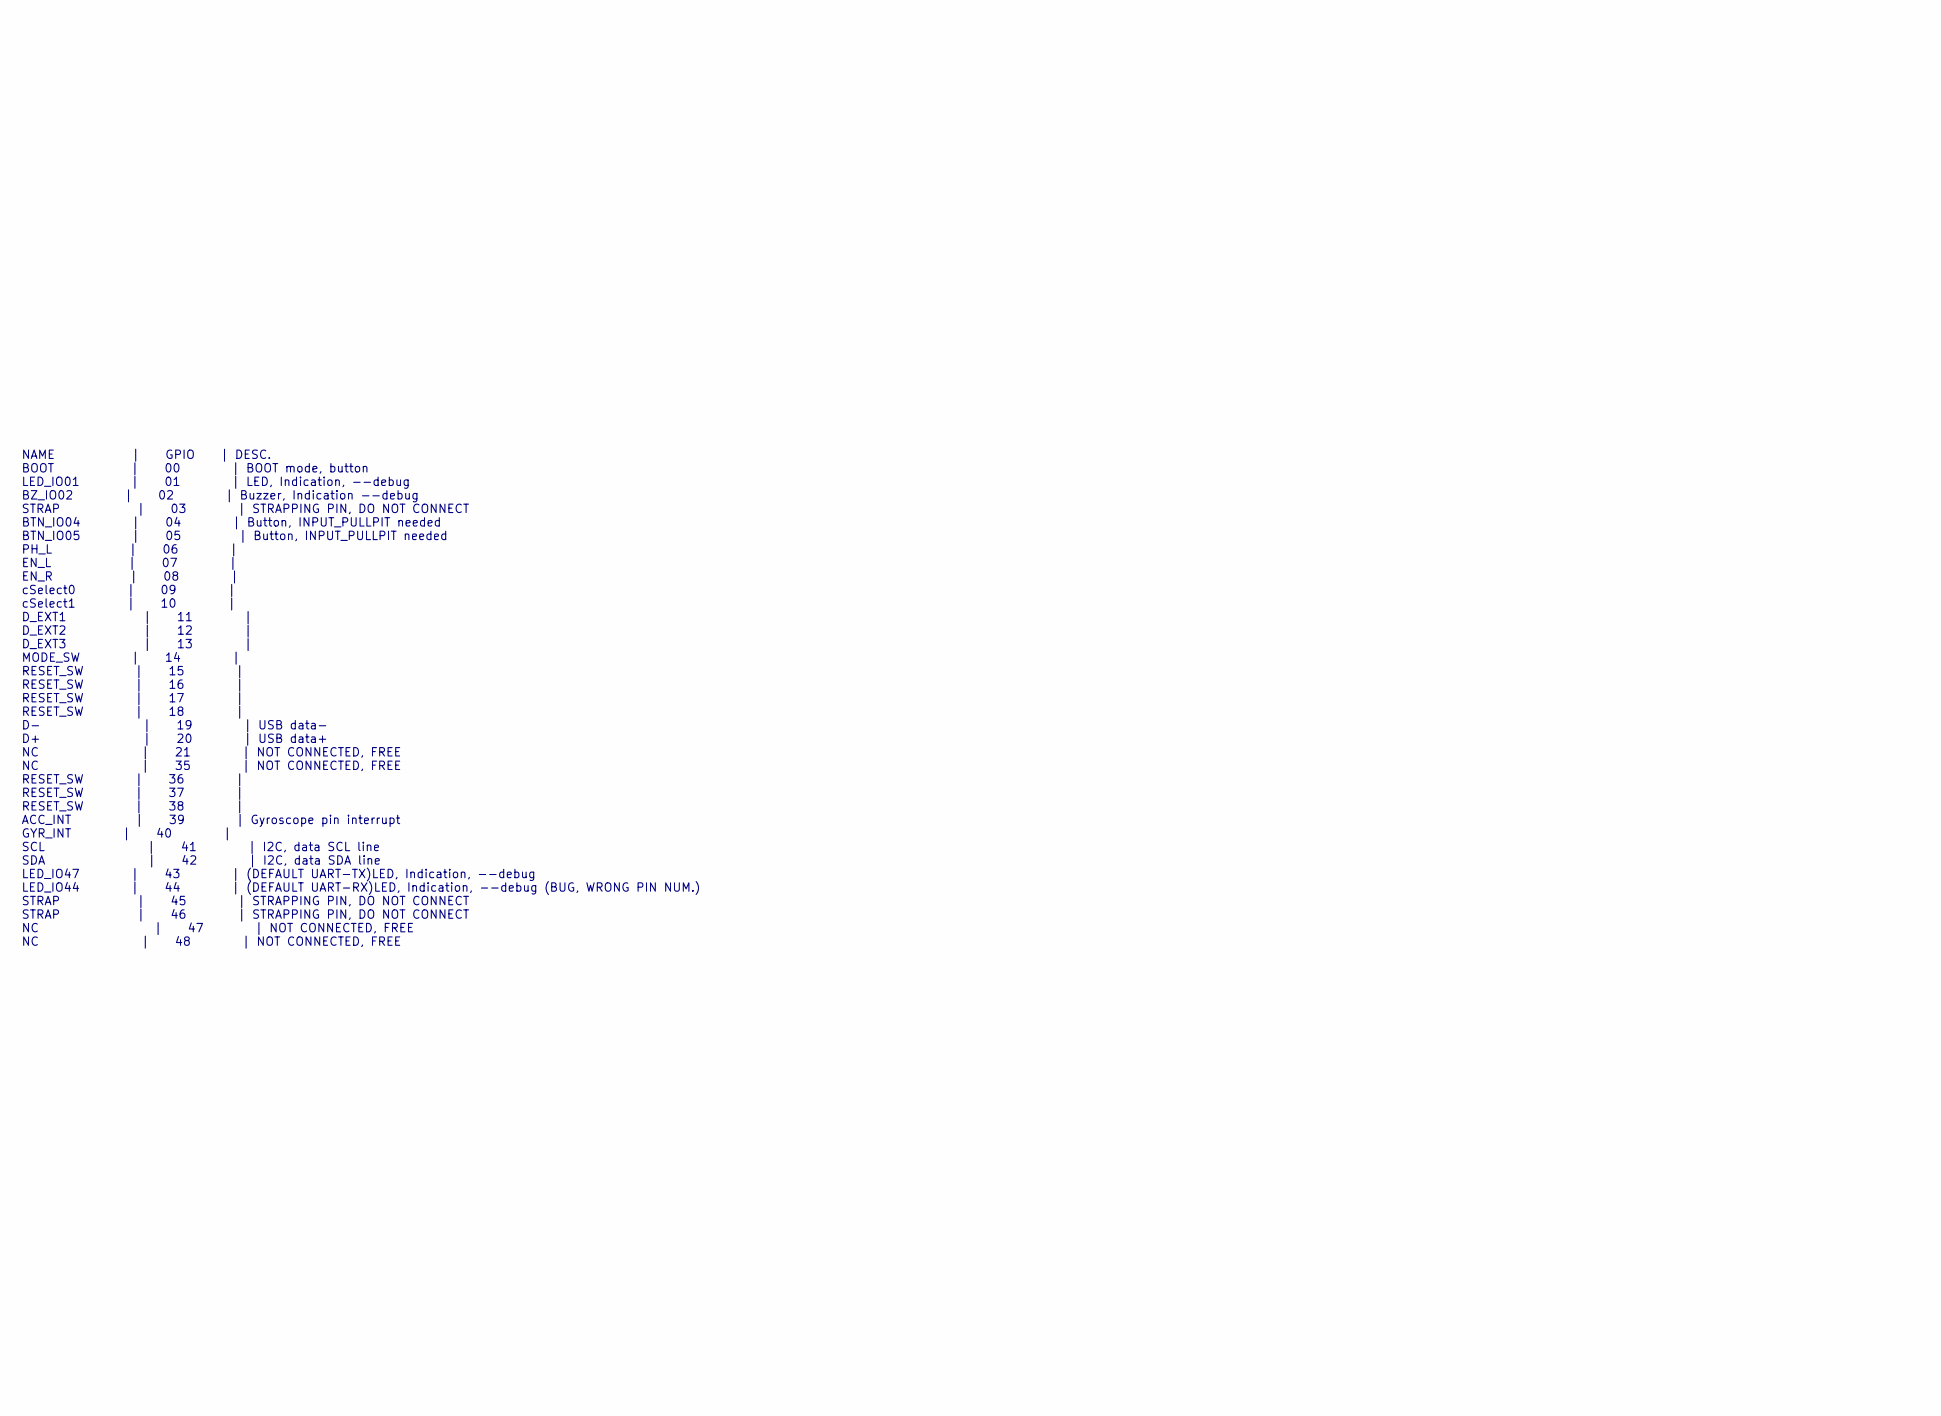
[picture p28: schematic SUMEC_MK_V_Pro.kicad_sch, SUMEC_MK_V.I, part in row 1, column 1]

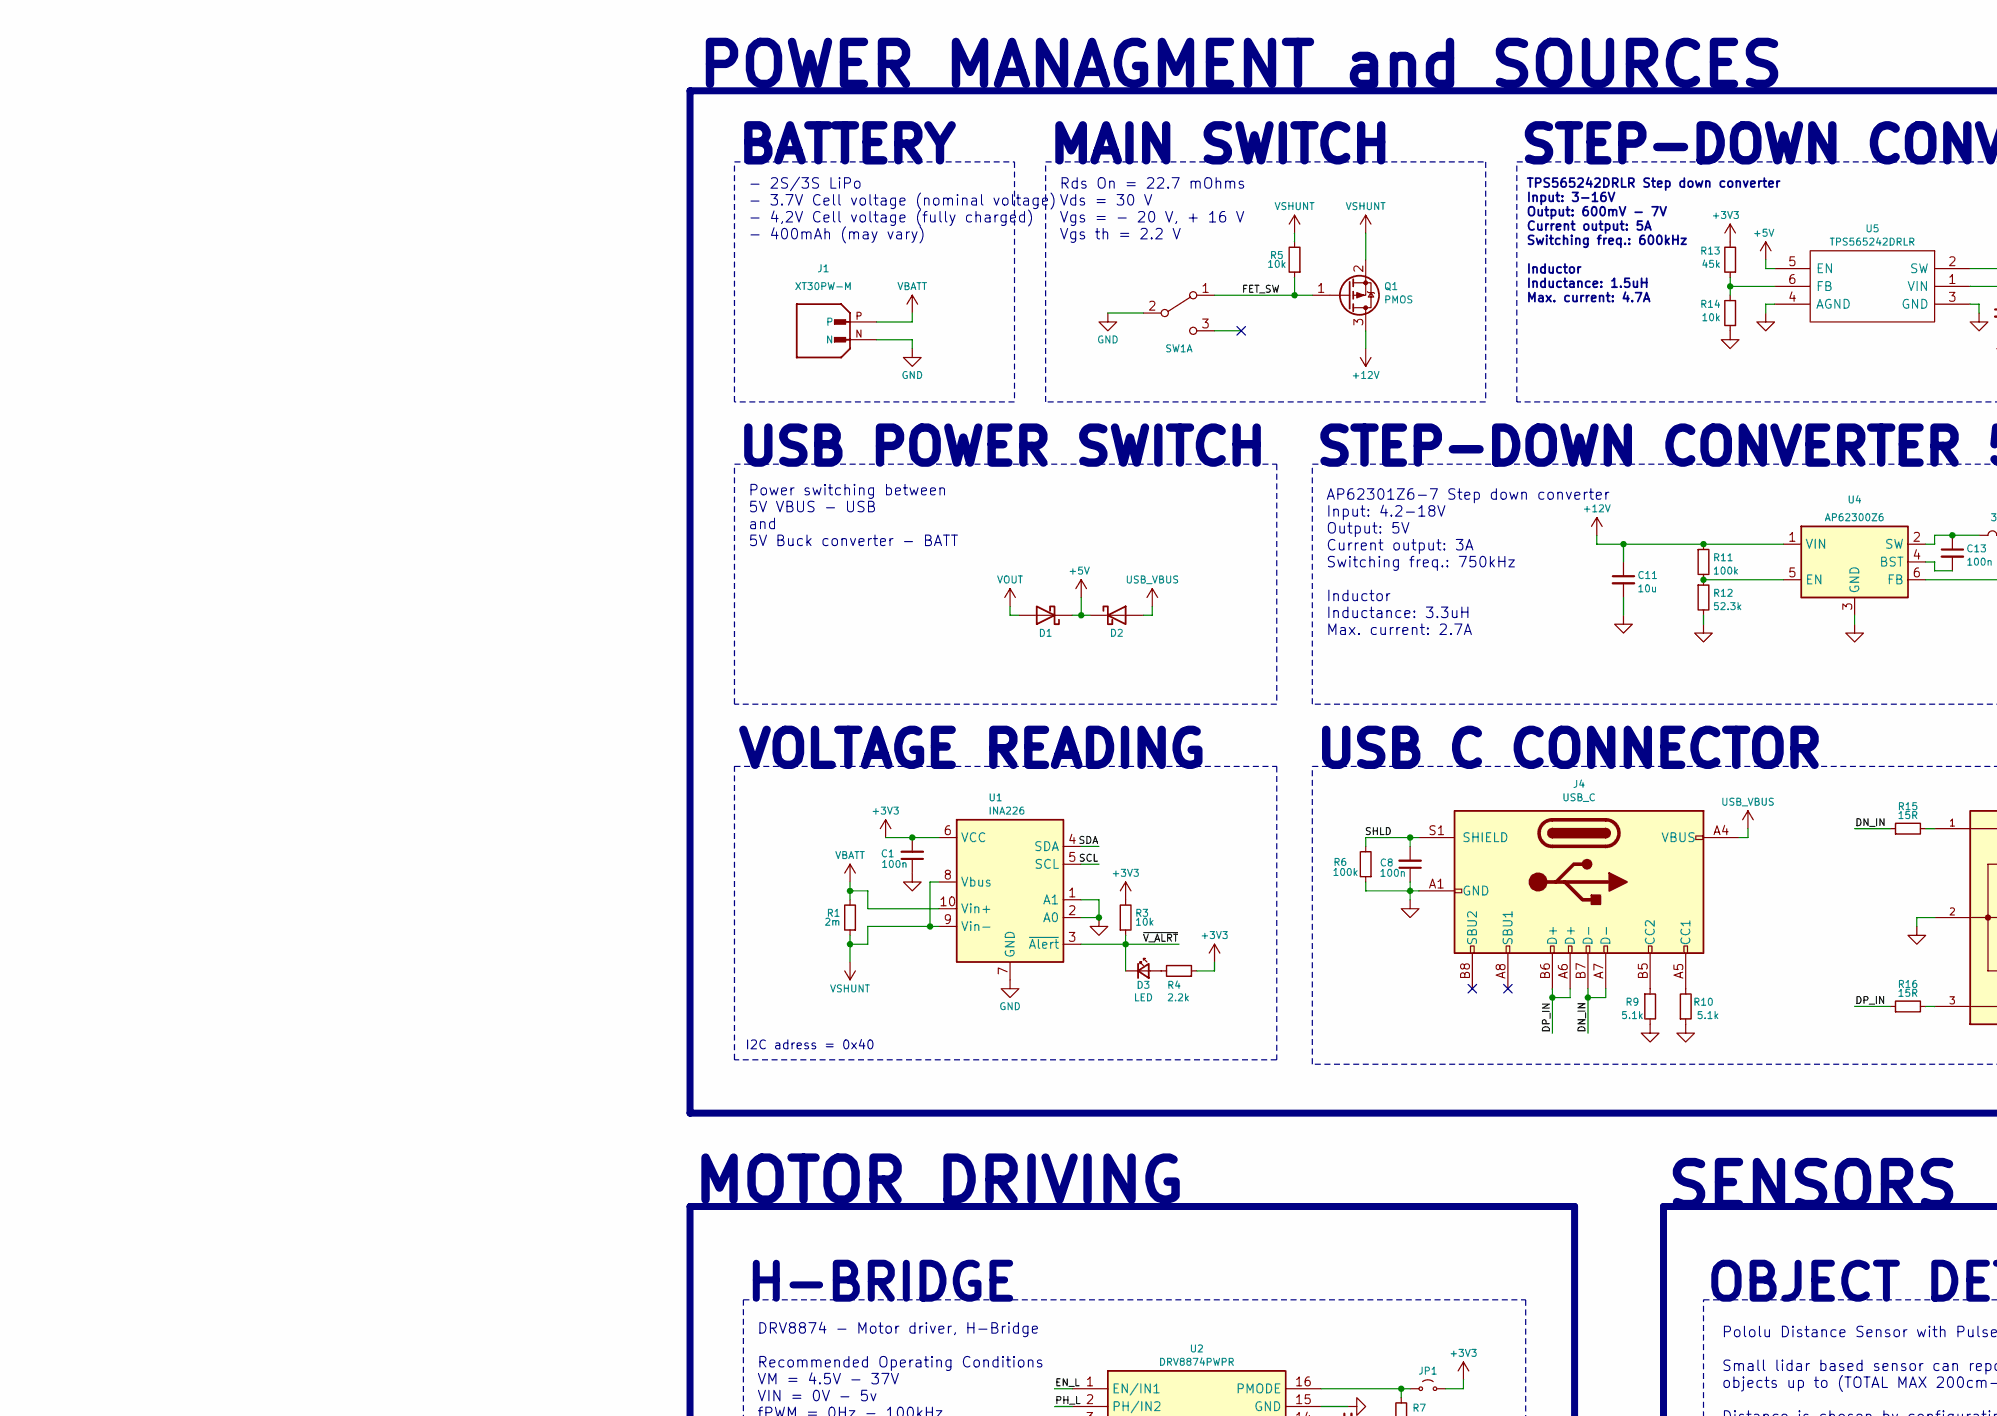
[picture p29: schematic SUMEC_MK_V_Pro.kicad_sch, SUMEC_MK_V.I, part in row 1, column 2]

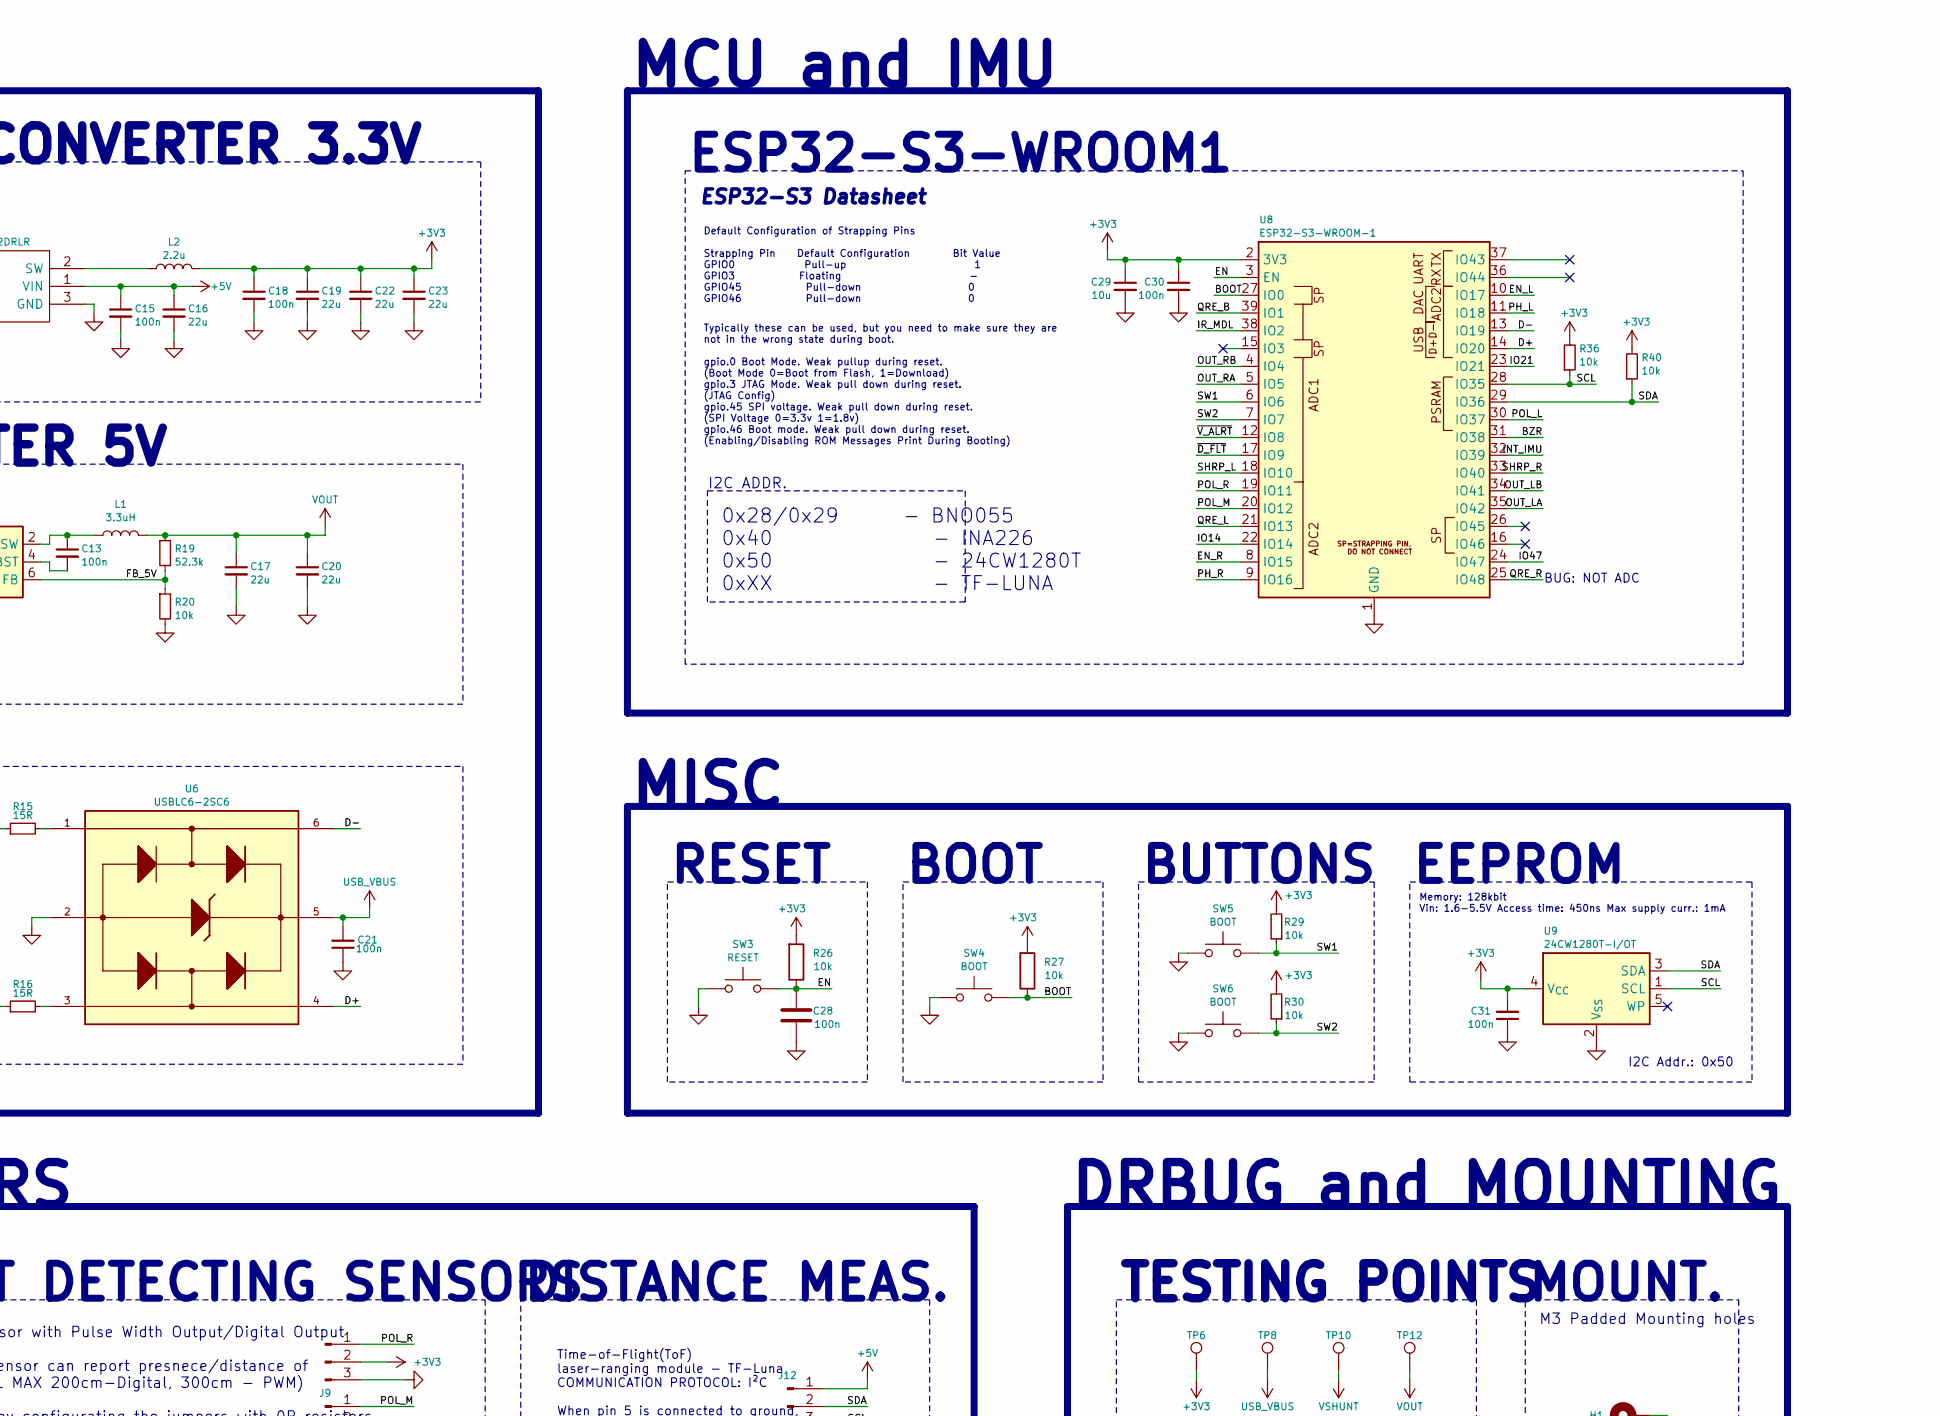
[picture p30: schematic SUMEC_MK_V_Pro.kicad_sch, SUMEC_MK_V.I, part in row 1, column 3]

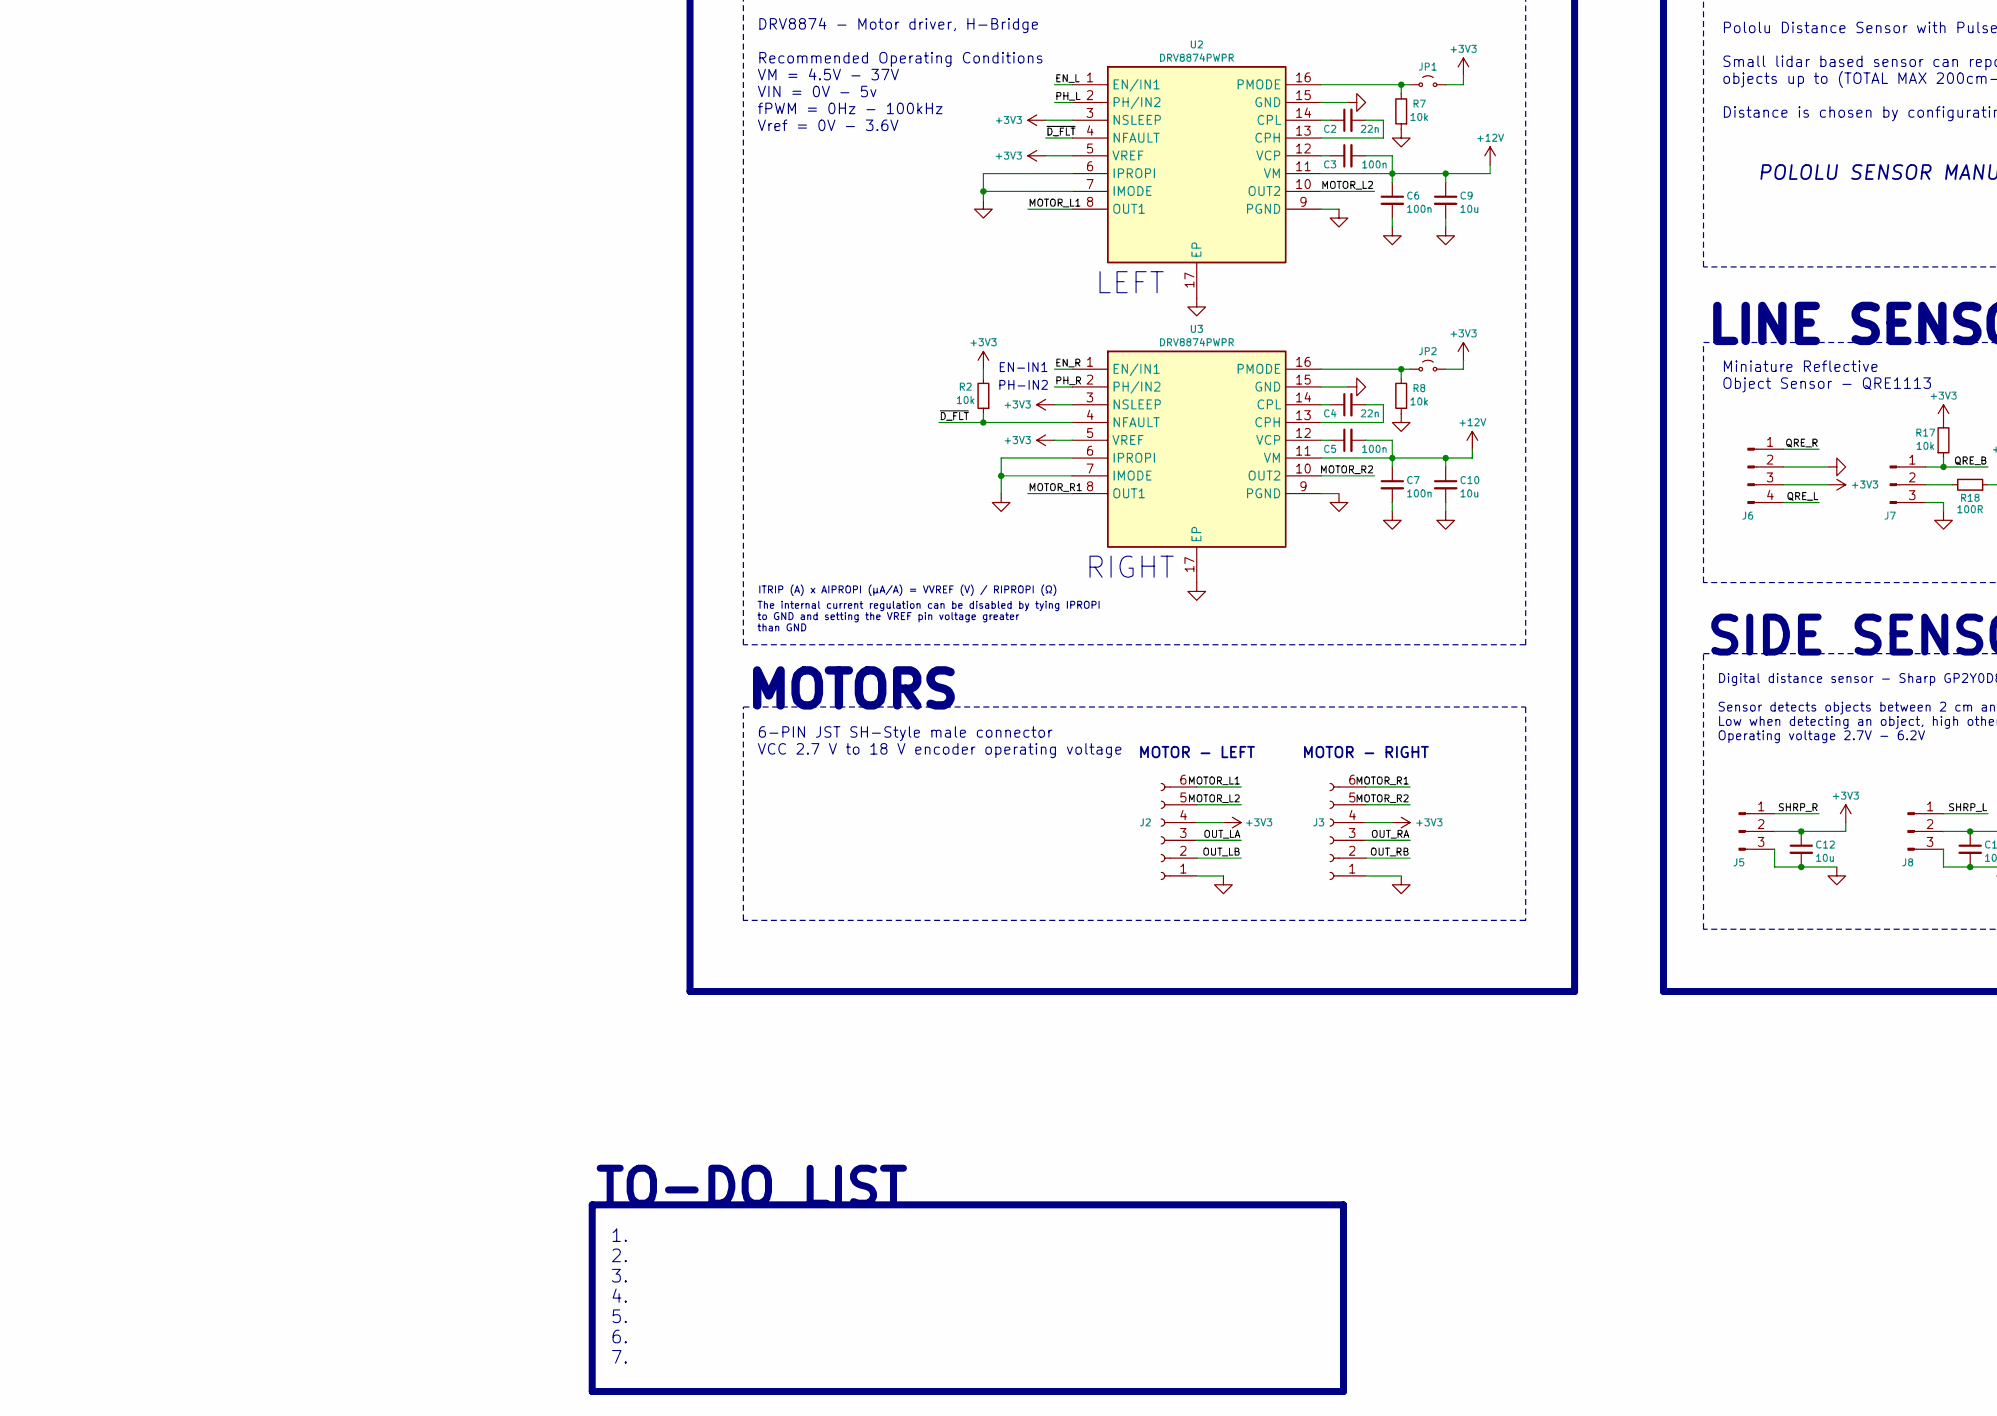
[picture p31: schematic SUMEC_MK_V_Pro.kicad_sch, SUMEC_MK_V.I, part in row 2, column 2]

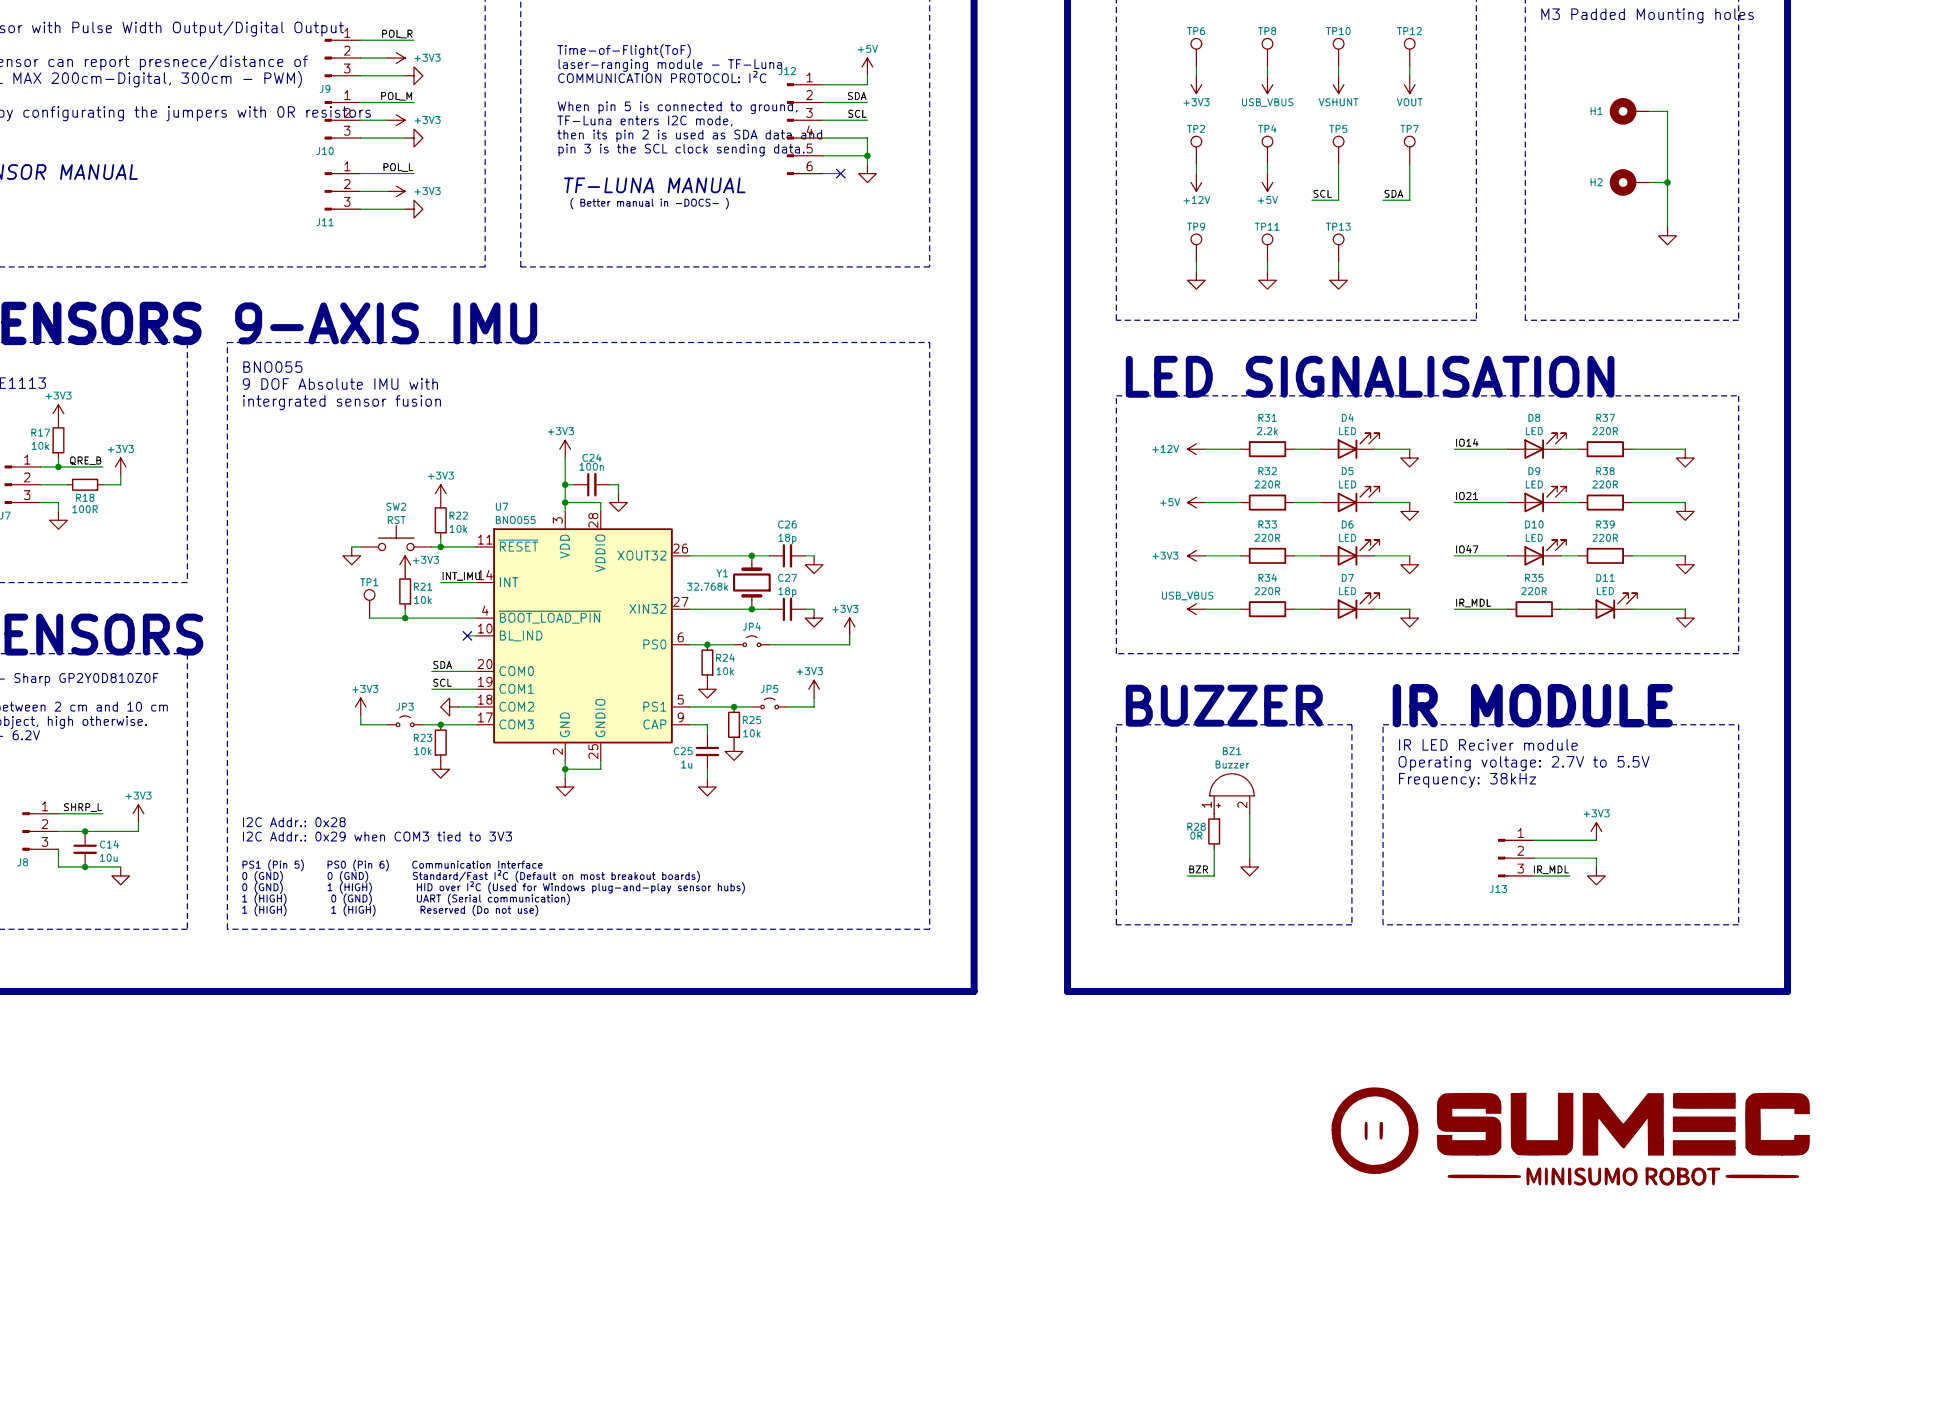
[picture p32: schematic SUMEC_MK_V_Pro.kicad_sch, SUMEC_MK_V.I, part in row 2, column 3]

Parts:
BZ1: Buzzer; BUZZER_CUI_CPT
C1, C3, C5, C6, C7, C8, C13, C15, C18, C21, C24, C28, C30, C31: 100n; C_0805_2012Metric
C2, C4: 22n; C_0805_2012Metric
C9, C10, C11, C12, C14, C29: 10u; C_0805_2012Metric
C16, C17, C19, C20, C22, C23: 22u; C_0805_2012Metric
C25: 1u; C_0805_2012Metric
C26, C27: 18p; C_0805_2012Metric
D1, D2: D_Schottky; D_1206_3216Metric
D3, D4, D5, D6, D7, D8, D9, D10, D11: LED; LED_0805_2012Metric
H1, H2: Mounting Hole M3; MountingHole_3.2mm_M3_Pad_Via
J1: XT30PW-M; PARTREV 1.2
J2, J3: Conn_01x06_Socket; JST_SH_BM06B-SRSS-TB_1x06-1MP_P1.00mm_Vertical
J4: USB_C; USB_C_Receptacle_GCT_USB4105-xx-A_16P_TopMnt_Horizontal
J5, J7, J8, J9, J10, J11: Conn_01x03_Pin; Molex_PicoBlade_53398-0371_1x03-1MP_P1.25mm_Vertical
J6: Conn_01x04_Pin; Molex_PicoBlade_53398-0471_1x04-1MP_P1.25mm_Vertical
J12: Conn_01x06_Pin; Molex_PicoBlade_53398-0671_1x06-1MP_P1.25mm_Vertical
J13: Conn_01x03_Pin; TerminalBlock_Phoenix_MPT-0,5-3-2.54_1x03_P2.54mm_Horizontal
JP1, JP2, JP3, JP4, JP5: Jumper_2_Small_Open; SolderJumper-2_P1.3mm_Open_RoundedPad1.0x1.5mm
L1: 3.3uH; L_Vishay_IHLP-1616
L2: 2.2u; L_Vishay_IHLP-1212
Q1: PMOS; SOT-23-3
R1: 2m; R_0805_2012Metric
R2, R3, R5, R7, R8, R14, R17, R20, R21, R22, R23, R24, R25, R26, R27, R29, R30, R36, R40: 10k; R_0805_2012Metric
R4, R31: 2.2k; R_0805_2012Metric
R6, R11: 100k; R_0805_2012Metric
R9, R10: 5.1k; R_0805_2012Metric
R12, R19: 52.3k; R_0805_2012Metric
R13: 45k; R_0805_2012Metric
R15, R16: 15R; R_0805_2012Metric
R18: 100R; R_0805_2012Metric
R28: 0R; R_0805_2012Metric
R32, R33, R34, R35, R37, R38, R39: 220R; R_0805_2012Metric
SW1: SW_DPDT_x2; Custom_SPDT_2.5_Switch
SW2: RST; SW_SPST_EVQPE1
SW3: RESET; SW_SPST_EVQPE1
SW4, SW5, SW6: BOOT; SW_SPST_EVQPE1
TP1, TP2, TP4, TP5, TP6, TP7, TP8, TP9, TP10, TP11, TP12, TP13: TestPoint; TestPoint_Pad_D1.5mm
U1: INA226; HVSSOP-10-1EP_3x3mm_P0.5mm_EP1.83x1.89mm
U2, U3: DRV8874PWPR; DRV8874; Manufacturer_Part_Number DRV8874PWPR; Mouser Part Number 595-DRV8874PWPR
U4: AP62300Z6; SOT-563
U5: TPS565242DRLR; SOT-563; Manufacturer_Part_Number TPS565242DRLR; Mouser Part Number 595-TPS565242DRLR
U6: USBLC6-2SC6; TSOT-23-6
U7: BNO055; LGA-28_5.2x3.8mm_P0.5mm
U8: ESP32-S3-WROOM-1
U9: 24CW1280T-I/OT; SOT-23-5
Y1: 32.768k; CM8V32768TA020125

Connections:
+3V3: C1.2, C12.1, C14.1, C18.1, C19.1, C22.1, C23.1, C24.1, C29.1, C30.1, C31.2, J2.4, J3.4, J5.2, J6.3, J8.2, J9.2, J10.2, J11.2, J13.1, JP1.2 (B), JP2.2 (B), JP3.2 (B), JP4.2 (B), JP5.2 (B), L2.2, R2.2, R3.2, R4.1, R13.2, R17.2, R18.1, R21.2, R22.2, R26.2, R27.2, R29.2, R30.2, R33.1, R36.2, R40.2, TP6.1 (1_1), U1.6 (VCC), U2.3 (NSLEEP), U2.5 (VREF), U3.3 (NSLEEP), U3.5 (VREF), U7.3 (VDD), U7.28 (VDDIO), U8.2 (3V3), U9.4 (V_{CC})
+5V: C15.1, C16.1, D1.1 (K), D2.1 (K), J12.1, R32.1, TP4.1 (1_1), U5.1 (VIN), U5.5 (EN)
+12V: C3.2, C5.2, C6.1, C7.1, C9.1, C10.1, C11.1, Q1.3 (D), R11.1, R31.1, TP2.1 (1_1), U2.11 (VM), U3.11 (VM), U4.1 (VIN)
/BOOT: R27.1, SW4.2, U8.27 (IO0)
/BZR: R28.2, U8.31 (IO38)
/D+: U6.4, U8.14 (IO20)
/D-: U6.6, U8.13 (IO19)
/DN_IN: J4.A7 (D-), J4.B7 (D-), R15.1
/DP_IN: J4.A6 (D+), J4.B6 (D+), R16.1
/EN: C28.2, R26.1, SW3.2, U8.3 (EN)
/EN_L: U2.1 (EN/IN1), U8.10 (IO17)
/EN_R: U3.1 (EN/IN1), U8.8 (IO15)
/FB_5V: R19.2, R20.1, U4.6 (FB)
/FET_SW: Q1.1 (G), R5.1, SW1.1 (A)
/INT_IMU: U7.14 (INT), U8.32 (IO39)
/IO14: D8.2 (A), U8.22 (IO14)
/IO21: D9.2 (A), U8.23 (IO21)
/IO47: D10.2 (A), U8.24 (IO47)
/IR_MDL: J13.3, R35.1, U8.38 (IO2)
/MOTOR_L1: J2.6, U2.8 (OUT1)
/MOTOR_L2: J2.5, U2.10 (OUT2)
/MOTOR_R1: J3.6, U3.8 (OUT1)
/MOTOR_R2: J3.5, U3.10 (OUT2)
/OUT_LA: J2.3, U8.35 (IO42)
/OUT_LB: J2.2, U8.34 (IO41)
/OUT_RA: J3.3, U8.5 (IO5)
/OUT_RB: J3.2, U8.4 (IO4)
/PH_L: U2.2 (PH/IN2), U8.11 (IO18)
/PH_R: U3.2 (PH/IN2), U8.9 (IO16)
/POL_L: J11.1, U8.30 (IO37)
/POL_M: J10.1, U8.20 (IO12)
/POL_R: J9.1, U8.19 (IO11)
/QRE_B: J7.1, R17.1, U8.39 (IO1)
/QRE_L: J6.4, U8.21 (IO13)
/QRE_R: J6.1, U8.25 (IO48)
/SCL: J12.3, R36.1, TP5.1 (1_1), U1.5 (SCL), U7.19 (COM1), U8.28 (IO35), U9.1 (SCL)
/SDA: J12.2, R40.1, TP7.1 (1_1), U1.4 (SDA), U7.20 (COM0), U8.29 (IO36), U9.3 (SDA)
/SHLD: C8.2, J4.S1 (SHIELD), R6.2
/SHRP_L: J8.1, U8.18 (IO10)
/SHRP_R: J5.1, U8.33 (IO40)
/SW1: R29.1, SW5.2, U8.6 (IO6)
/SW2: R30.1, SW6.2, U8.7 (IO7)
/~D_FLT: R2.1, U2.4 (NFAULT), U3.4 (NFAULT), U8.17 (IO9)
/~V_ALRT: D3.1 (K), R3.1, U1.3 (~Alert), U8.12 (IO8)
GND: BZ1.2 (-), C1.1, C6.2, C7.2, C8.1, C9.2, C10.2, C11.2, C12.2, C14.2, C15.2, C16.2, C17.2, C18.2, C19.2, C20.2, C21.1, C22.2, C23.2, C24.2, C25.2, C26.2, C27.2, C28.1, C29.2, C30.2, C31.1, D4.1 (K), D5.1 (K), D6.1 (K), D7.1 (K), D11.1 (K), H1.1 (1_1), H2.1 (1_1), J1.N, J2.1, J3.1, J4.A1 (GND), J4.A12 (GND), J4.B1 (GND), J4.B12 (GND), J5.3, J6.2, J7.3, J8.3, J9.3, J10.3, J11.3, J12.4, J12.5, J13.2, R6.1, R7.1, R8.1, R9.2, R10.1, R12.2, R14.1, R20.2, R23.1, R24.1, R25.1, R37.2, R38.2, R39.2, SW1.2 (B), SW2.1, SW3.1, SW4.1, SW5.1, SW6.1, TP9.1 (1_1), TP11.1 (1_1), TP13.1 (1_1), U1.1 (A1), U1.2 (A0), U1.7 (GND), U2.6 (IPROPI), U2.7 (IMODE), U2.9 (PGND), U2.15 (GND), U2.17 (EP), U3.6 (IPROPI), U3.7 (IMODE), U3.9 (PGND), U3.15 (GND), U3.17 (EP), U4.3 (GND), U5.3 (GND), U5.4 (AGND), U6.2, U7.2 (GND), U7.18 (COM2), U7.25 (GNDIO), U8.1 (GND), U8.40 (GND), U8.41 (GND), U9.2 (V_{SS})
unnamed: BZ1.1 (+), R28.1
unnamed: D3.2 (A), R4.2
unnamed: D4.2 (A), R31.2
unnamed: D5.2 (A), R32.2
unnamed: D6.2 (A), R33.2
unnamed: D7.2 (A), R34.2
unnamed: D8.1 (K), R37.1
unnamed: D9.1 (K), R38.1
unnamed: D10.1 (K), R39.1
unnamed: D11.2 (A), R35.2
unnamed: J4.A5 (CC1), R10.2
unnamed: J4.B5 (CC2), R9.1
unnamed: J7.2, R18.2
unnamed: JP1.1 (A), R7.2, U2.16 (PMODE)
unnamed: JP2.1 (A), R8.2, U3.16 (PMODE)
unnamed: JP3.1 (A), R23.2, U7.17 (COM3)
unnamed: JP4.1 (A), R24.2, U7.6 (PS0)
unnamed: JP5.1 (A), R25.2, U7.5 (PS1)
unnamed: R15.2, U6.1
unnamed: R16.2, U6.3
unnamed: C2.2, U2.13 (CPH)
unnamed: C2.1, U2.14 (CPL)
unnamed: C3.1, U2.12 (VCP)
unnamed: C4.2, U3.13 (CPH)
unnamed: C4.1, U3.14 (CPL)
unnamed: C5.1, U3.12 (VCP)
unnamed: C13.2, U4.4 (BST)
unnamed: R11.2, R12.1, U4.5 (EN)
unnamed: C13.1, L1.1, U4.2 (SW)
unnamed: R13.1, R14.2, U5.6 (FB)
unnamed: L2.1, U5.2 (SW)
unnamed: C25.1, U7.9 (CAP)
unnamed: C27.1, U7.27 (XIN32), Y1.1
unnamed: C26.1, U7.26 (XOUT32), Y1.2
unnamed: R21.1, TP1.1 (1_1), U7.4 (~BOOT_LOAD_PIN)
unnamed: R22.1, SW2.2, U7.11 (~RESET)
USB_VBUS: C21.2, D2.2 (A), J4.A4 (VBUS), J4.A9 (VBUS), J4.B4 (VBUS), J4.B9 (VBUS), R34.1, TP8.1 (1_1), U6.5
VBATT: J1.P, R1.2, U1.10 (Vin+)
VOUT: C17.1, C20.1, D1.2 (A), L1.2, R19.1, TP12.1 (1_1)
VSHUNT: Q1.2 (S), R1.1, R5.2, TP10.1 (1_1), U1.8 (Vbus), U1.9 (Vin-)

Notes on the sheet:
Default Configuration of Strapping Pins Strapping Pin Default Configuration Bit Value GPIO0 Pull-up 1 GPIO3 Floating - GPIO45 Pull-down 0 GPIO46 Pull-down 0
IR LED Reciver module Operating voltage: 2.7V to 5.5V Frequency: 38kHz
M3 Padded Mounting holes
STEP-DOWN CONVERTER 5V
6-PIN JST SH-Style male connector VCC 2.7 V to 18 V encoder operating voltage
AP62301Z6-7 Step down converter Input: 4.2-18V Output: 5V Current output: 3A Switching freq.: 750kHz Inductor Inductance: 3.3uH Max. current: 2.7A
LEFT
BUZZER
0x28/0x29 - BNO055 0x40 - INA226 0x50 - 24CW1280T 0xXX - TF-LUNA
SENSORS
TF-LUNA MANUAL
I2C Addr.: 0x50
( Better manual in -DOCS- )
STEP-DOWN CONVERTER 3.3V
OBJECT DETECTING SENSORS
PS1 (Pin 5) PS0 (Pin 6) Communication Interface 0 (GND) 0 (GND) Standard/Fast I²C (Default on most breakout boards) 0 (GND) 1 (HIGH) HID over I²C (Used for Windows plug-and-play sensor hubs) 1 (HIGH) 0 (GND) UART (Serial communication) 1 (HIGH) 1 (HIGH) Reserved (Do not use)
Digital distance sensor - Sharp GP2Y0D810Z0F Sensor detects objects between 2 cm and 10 cm Low when detecting an object, high otherwise. Operating voltage 2.7V - 6.2V
MOTOR - RIGHT
TPS565242DRLR Step down converter Input: 3-16V Output: 600mV - 7V Current output: 5A Switching freq.: 600kHz Inductor Inductance: 1.5uH Max. current: 4.7A
I2C ADDR.
EEPROM
MOUNT.
BNO055 9 DOF Absolute IMU with intergrated sensor fusion
VOLTAGE READING
Rds On = 22.7 mOhms Vds = 30 V Vgs = - 20 V, + 16 V Vgs th = 2.2 V
NAME | GPIO | DESC. BOOT | 00 | BOOT mode, button LED_IO01 | 01 | LED, Indication, --debug BZ_IO02 | 02 | Buzzer, Indication --debug STRAP | 03 | STRAPPING PIN, DO NOT CONNECT BTN_IO04 | 04 | Button, INPUT_PULLPIT needed BTN_IO05 | 05 | Button, INPUT_PULLPIT needed PH_L | 06 | EN_L | 07 | EN_R | 08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
I2C Addr.: 0x28 I2C Addr.: 0x29 when COM3 tied to 3V3
MAIN SWITCH
MOTOR - LEFT
- 2S/3S LiPo - 3.7V Cell voltage (nominal voltage) - 4,2V Cell voltage (fully charged) - 400mAh (may vary)
DRBUG and MOUNTING
LED SIGNALISATION
Pololu Distance Sensor with Pulse Width Output/Digital Output Small lidar based sensor can report presnece/distance of objects up to (TOTAL MAX 200cm-Digital, 300cm - PWM) Distance is chosen by configurating the jumpers with 0R resistors
EN-IN1
ITRIP (A) x AIPROPI (μA/A) = VVREF (V) / RIPROPI (Ω)
MOTORS
9-AXIS IMU
TO-DO LIST
MISC
I2C adress = 0x40

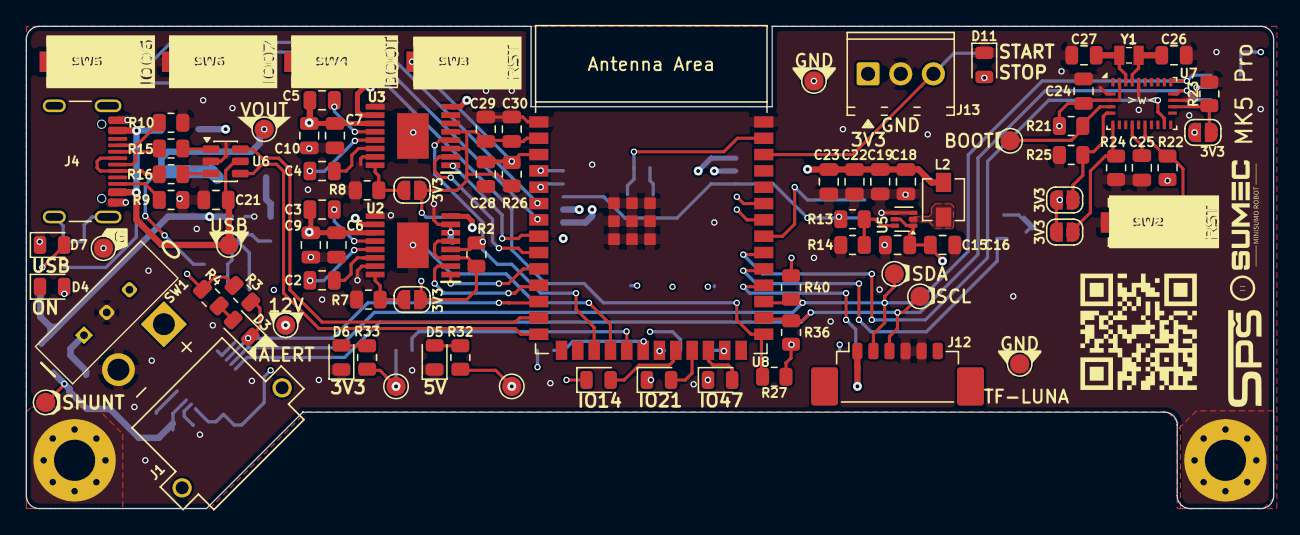
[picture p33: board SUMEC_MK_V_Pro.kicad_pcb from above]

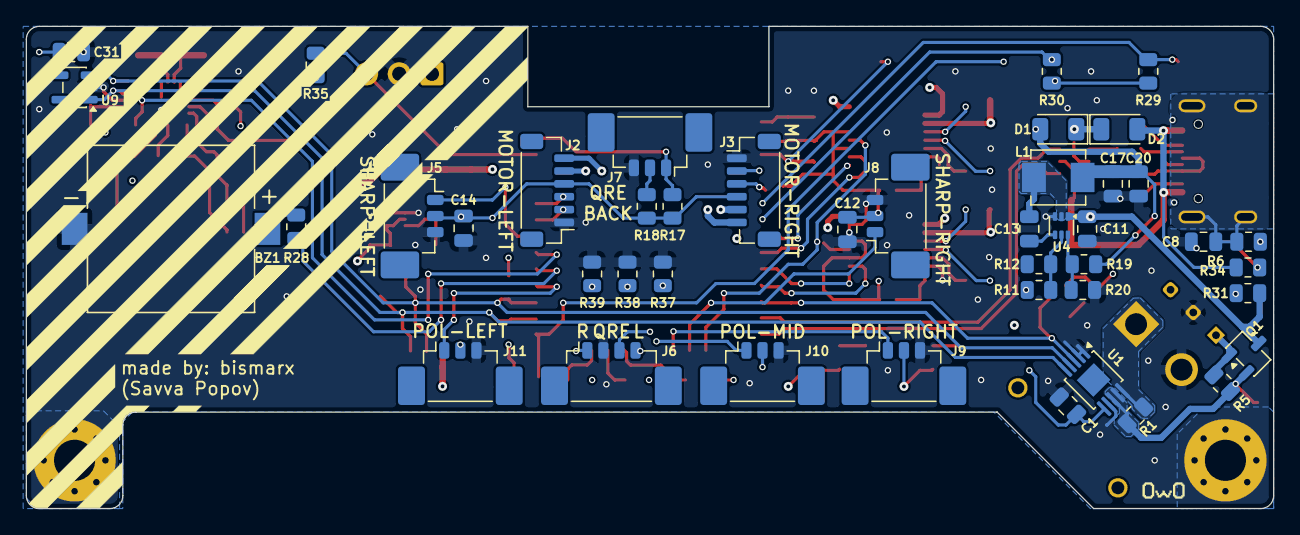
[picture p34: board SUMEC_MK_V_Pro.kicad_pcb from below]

Board: 4 copper layers, 97.0 x 37.5 mm, 137 parts (44 on the bottom side), 85 nets.

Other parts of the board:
TP1#2: TestPoint; SUMEC_QR_IMG
TP2#2: TestPoint; SPS_LOGO_IMG
TP3: TestPoint; SUMEC_LOGO_IMG

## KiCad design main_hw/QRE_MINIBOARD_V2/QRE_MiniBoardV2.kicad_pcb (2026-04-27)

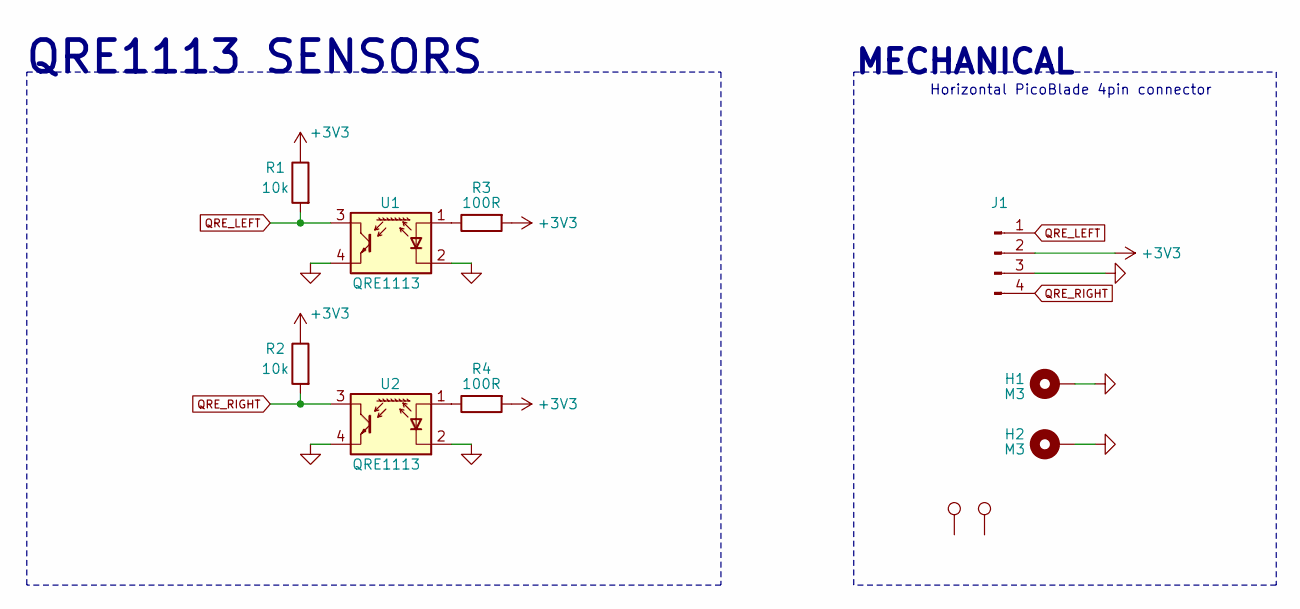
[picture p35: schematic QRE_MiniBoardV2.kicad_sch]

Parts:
H1, H2: M3; MountingHole_3.2mm_M3_Pad_Via
J1: Conn_01x04_Pin; Molex_PicoBlade_53261-0471_1x04-1MP_P1.25mm_Horizontal
R1, R2: 10k; R_0805_2012Metric_Pad1.20x1.40mm_HandSolder
R3, R4: 100R; R_0805_2012Metric_Pad1.20x1.40mm_HandSolder
TP1: TestPoint; BOYKISSER_IMG
TP2: TestPoint; OWO_IMG
U1, U2: QRE1113; OnSemi_CASE100CY

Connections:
+3V3: J1.2, R1.1, R2.1, R3.2, R4.2
GND: H1.1, H2.1, J1.3, U1.2 (K), U1.4, U2.2 (K), U2.4
unnamed: R3.1, U1.1 (A)
unnamed: R4.1, U2.1 (A)
QRE_LEFT: J1.1, R1.2, U1.3
QRE_RIGHT: J1.4, R2.2, U2.3

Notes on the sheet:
QRE1113 SENSORS
Horizontal PicoBlade 4pin connector
MECHANICAL

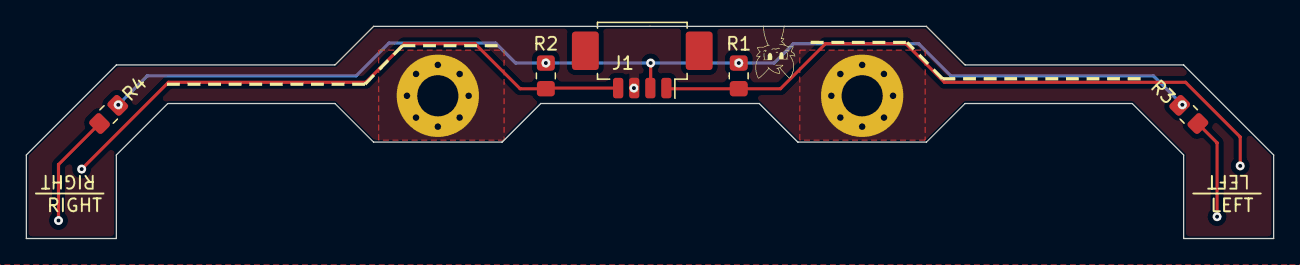
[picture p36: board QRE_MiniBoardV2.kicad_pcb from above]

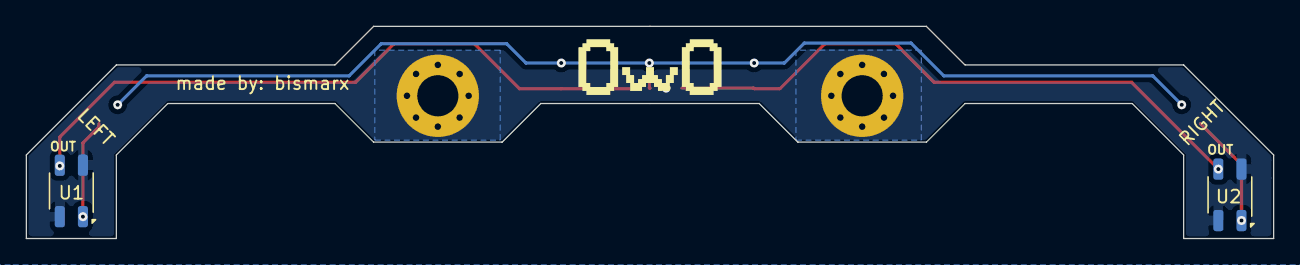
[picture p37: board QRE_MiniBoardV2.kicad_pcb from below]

Board: 2 copper layers, 97.0 x 16.5 mm, 11 parts (3 on the bottom side), 6 nets.

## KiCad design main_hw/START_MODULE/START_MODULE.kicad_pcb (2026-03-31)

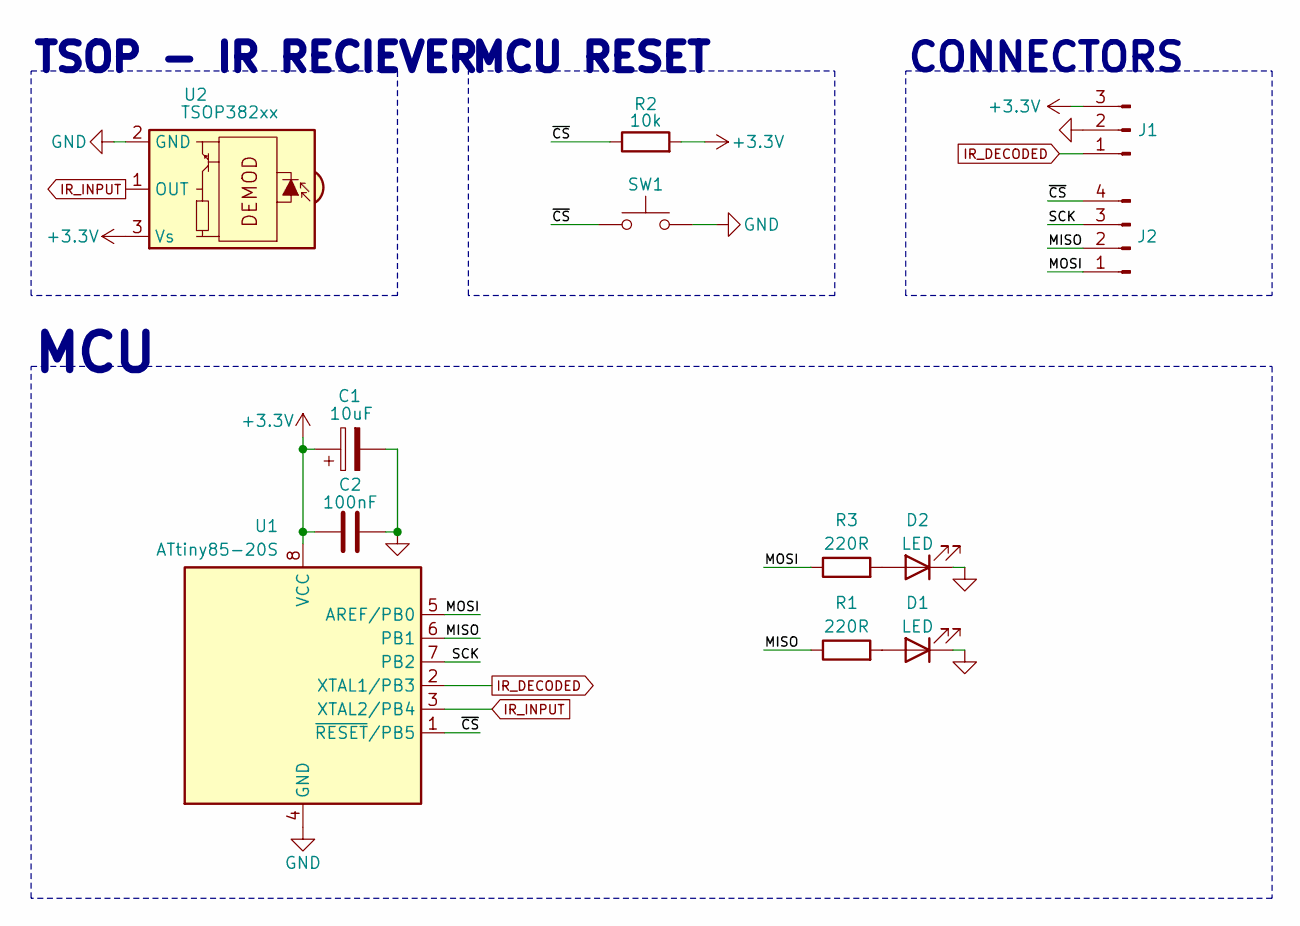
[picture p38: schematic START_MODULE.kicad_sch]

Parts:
C1: 10uF; CP_EIA-3216-18_Kemet-A_Pad1.58x1.35mm_HandSolder
C2: 100nF; C_0805_2012Metric_Pad1.18x1.45mm_HandSolder
D1, D2: LED; LED_0805_2012Metric_Pad1.15x1.40mm_HandSolder
J1: Conn_01x03_Pin; PinHeader_1x03_P2.54mm_Horizontal
J2: Conn_01x04_Pin; PinHeader_1x04_P2.54mm_Vertical
R1, R3: 220R; R_0805_2012Metric_Pad1.20x1.40mm_HandSolder
R2: 10k; R_0805_2012Metric_Pad1.20x1.40mm_HandSolder
SW1: SW_Push; SW_SPST_EVQPE1
U1: ATtiny85-20S; SOIC-8W_5.3x5.3mm_P1.27mm
U2: TSOP382xx; Vishay_MINICAST-3Pin

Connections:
+3.3V: C1.1, C2.1, J1.3, R2.2, U1.8 (VCC), U2.3 (Vs)
/MISO: J2.2, R1.1, U1.6 (PB1)
/MOSI: J2.1, R3.1, U1.5 (AREF/PB0)
/SCK: J2.3, U1.7 (PB2)
/~CS: J2.4, R2.1, SW1.2, U1.1 (~RESET/PB5)
GND: C1.2, C2.2, D1.1 (K), D2.1 (K), J1.2, SW1.1, U1.4 (GND), U2.2 (GND)
IR_DECODED: J1.1, U1.2 (XTAL1/PB3)
IR_INPUT: U1.3 (XTAL2/PB4), U2.1 (OUT)
unnamed: D1.2 (A), R1.2
unnamed: D2.2 (A), R3.2

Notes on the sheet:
MCU
TSOP - IR RECIEVER
CONNECTORS
MCU RESET

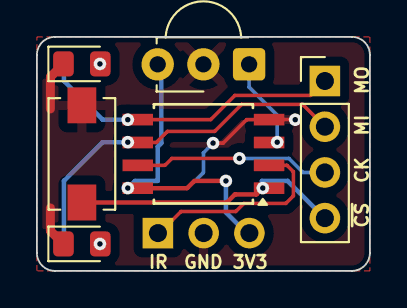
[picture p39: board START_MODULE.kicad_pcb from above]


Board: 2 copper layers, 18.5 x 13.0 mm, 12 parts (6 on the bottom side), 10 nets.

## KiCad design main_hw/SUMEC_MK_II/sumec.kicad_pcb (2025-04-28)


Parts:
R1: R; logo even smaller
R2: R; car cool smol

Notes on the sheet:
ESP32-S3 Datasheet


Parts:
H1, H2, H3, H4: MountingHole M3; MountingHole_3.2mm_M3_ISO7380_Pad
J1: Conn_01x04_Pin; PinHeader_1x04_P2.54mm_Vertical
J2: Conn_01x01_Pin; SolderWire-0.1sqmm_1x01_D0.4mm_OD1mm
J3: Conn_01x03_Pin; PinSocket_1x03_P2.54mm_Vertical
J4: Conn_01x02; PinHeader_1x02_P2.54mm_Vertical
SW1: SW_Push; SW_SPST_B3U-1000P

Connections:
+3V3: J3.3, SW1.1; also elsewhere on the board
+8V: J4.1; also elsewhere on the board
GND: J3.2; also elsewhere on the board
MOTOR 1 +: J1.1; also elsewhere on the board
MOTOR 1 -: J1.2; also elsewhere on the board
MOTOR 2 +: J1.4; also elsewhere on the board
MOTOR 2 -: J1.3; also elsewhere on the board
QRE1113 A: J3.1; also elsewhere on the board
TEST PROGRAM: SW1.2; also elsewhere on the board
VBATT: J4.2; also elsewhere on the board
VBUS 5V: J2.1; also elsewhere on the board

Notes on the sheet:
MOUNTING HOLES
Pads for connecting motors and rivets
Mounting holes M3 Mounting holes that are screwed to the heat-inserts on the chassis
MAIN SWITCH
TEST TLAČITKO
Main switch is connected via two wires for easy access.
PADY a PROKOVY
Tactile swicth (button) Used for starting test code program LED is used as indicator of starting the said program - (subjcet to change depending on different usage of LED, for example; multiple flashing for trouble-shooting or indicating)





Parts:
C1: 10uF.hb; C_1206_3216Metric
C2: 1uF.hb; C_1206_3216Metric
C3: 10uF.mcu; C_1206_3216Metric
C4: 100nF.mcu; C_1206_3216Metric
C5: 10uF.hbc; C_1206_3216Metric
C6: 100nF.hbc; C_1206_3216Metric
C7: 100nF.en; C_1206_3216Metric
C8: 100nF.boot; C_1206_3216Metric
C9: 100nF; C_1206_3216Metric
D1: LED; LED_1206_3216Metric_Pad1.42x1.75mm_HandSolder
D2: 1N5819; D_1206_3216Metric
J5: TYPE-C-31-M-12; HRO_TYPE-C-31-M-12; PARTREV 2020.12.08
R3: 220; R_1206_3216Metric_Pad1.30x1.75mm_HandSolder
R4: 0R; R_1206_3216Metric
R5, R6: 15R; R_1206_3216Metric
R7: 10k.mcu; R_1206_3216Metric
SW2, SW3: SW_Push; SW_SPST_B3U-1000P
U1: TB6612FNG; SSOP-24_5.3x8.2mm_P0.65mm
U2: ESP32-S3-WROOM-1
U3: USBLC6-2SC6; TSOT-23-6_HandSoldering

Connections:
+3V3: C1.1, C2.1, C3.1, C4.1, R7.2, U1.20 (VCC), U2.2 (3V3); also elsewhere on the board
+8V: C5.1, C6.1, U1.13 (VM2), U1.14 (VM3), U1.24 (VM1); also elsewhere on the board
AI1: U1.21 (AIN1), U2.18 (GPIO10/TOUCH10/ADC1_CH9/FSPICS0/FSPIIO4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)
AI2: U1.22 (AIN2), U2.17 (GPIO9/TOUCH9/ADC1_CH8/FSPIHD/SUBSPIHD)
BI1: U1.17 (BIN1), U2.21 (GPIO13/TOUCH13/ADC2_CH2/FSPIQ/FSPIIO7/S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)
BI2: U1.16 (BIN2), U2.22 (GPIO14/TOUCH14/ADC2_CH3/FSPIWP/FSPIDQS/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)
BOOT: C8.1, SW3.2, U2.27 (GPIO0/BOOT)
D+: U2.14 (GPIO20/U1CTS/ADC2_CH9/CLK_OUT1/USB_D+), U3.6
D+ IN: J5.A6 (DP1), J5.B6 (DP2), R5.1
D-: U2.13 (GPIO19/U1RTS/ADC2_CH8/CLK_OUT2/USB_D-), U3.4
D- IN: J5.A7 (DN1), J5.B7 (DN2), R6.1
EN: C7.1, R7.1, SW2.2, U2.3 (EN)
GND: C1.2, C2.2, C3.2, C4.2, C5.2, C6.2, C7.2, C8.2, C9.2, J5.A1_B12 (GND), J5.B1_A12 (GND), R3.2, R4.2, SW2.1, SW3.1, U1.3 (PGND1), U1.4 (PGND1), U1.9 (PGND2), U1.10 (PGND2), U1.18 (GND), U2.1 (GND), U2.40 (GND), U2.41 (GND), U3.2; also elsewhere on the board
IR MODULE: U2.31 (GPIO38/FSPIWP/SUBSPIWP); also elsewhere on the board
LED: D1.2 (A), U2.8 (GPIO15/U0RTS/ADC2_CH4/XTAL_32K_P)
MOTOR 1 +: U1.1 (AO1), U1.2 (AO1); also elsewhere on the board
MOTOR 1 -: U1.5 (AO2), U1.6 (AO2); also elsewhere on the board
MOTOR 2 +: U1.11 (BO1), U1.12 (BO1); also elsewhere on the board
MOTOR 2 -: U1.7 (BO2), U1.8 (BO2); also elsewhere on the board
unnamed: D1.1 (K), R3.1
unnamed: D2.2 (A), J5.A4_B9 (VBUS), J5.B4_A9 (VBUS)
unnamed: J5.S1 (SHIELD), J5.S2 (SHIELD), J5.S3 (SHIELD), J5.S4 (SHIELD), R4.1
unnamed: R5.2, U3.1
unnamed: R6.2, U3.3
PWMA: U1.23 (PWMA), U2.19 (GPIO11/TOUCH11/ADC2_CH0/FSPID/FSPIIO5/S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)
PWMB: U1.15 (PWMB), U2.23 (GPIO21)
QRE1113 A: U2.4 (GPIO4/TOUCH4/ADC1_CH3); also elsewhere on the board
QRE1113 B: U2.7 (GPIO7/TOUCH7/ADC1_CH6); also elsewhere on the board
QRE1113 C: U2.6 (GPIO6/TOUCH6/ADC1_CH5); also elsewhere on the board
QRE1113 D: U2.5 (GPIO5/TOUCH5/ADC1_CH4); also elsewhere on the board
SCL: U2.10 (GPIO17/U1TXD/ADC2_CH6); also elsewhere on the board
SDA: U2.11 (GPIO18/U1RXD/ADC2_CH7/CLK_OUT3); also elsewhere on the board
STBY: U1.19 (STBY), U2.20 (GPIO12/TOUCH12/ADC2_CH1/FSPICLK/FSPIIO6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)
TEST PROGRAM: U2.38 (GPIO2/TOUCH2/ADC1_CH1); also elsewhere on the board
VBUS 5V: C9.1, D2.1 (K), U3.5; also elsewhere on the board
X-SHUT1: U2.33 (MTDO/GPIO40/CLK_OUT2); also elsewhere on the board
X-SHUT2: U2.34 (MTDI/GPIO41/CLK_OUT1); also elsewhere on the board
X-SHUT3: U2.35 (MTMS/GPIO42); also elsewhere on the board

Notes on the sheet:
ADC1
USB
I2C
SPI voltage
Enable (EN) is the 3.3V regulator’s enable pin. It’s pulled up, so connect to ground to disable the 3.3V regulator. This means that you can use this pin connected to a pushbutton to restart your ESP32, for example.
USB CONNECTOR
USB Type-C Connector
GPIO0, GPIO45, and GPIO46 are connected to the chip's internal weak pull-up/pull-down resistors at chip reset. These resistors determine the default bit values of the strapping pins. Also, these resistors determine the bit values if the strapping pins are connected to an external high-impedance cir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
ENABLE
GPIO USB 20 D+ (green) 19 D- (white) GND GND (black) NC +5V (red)
H-MŮSTEK
Status LED
BOOT mode
If the device does not support the auto download mode, you need to get into the download mode manually. To do so, press and hold the BOOT button and then press the RESET button once. After that release the BOOT button.
Motor Driver - TB6612FNG (IN1 and IN2) can be used to control the motor in one of four function modes: - CW, CCW, short-brake and stop. The two motor outputs (A and B) can be separately controlled, and the speed of each motor is controlled via a PWM input signal with a frequency up to 100kHz. The S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
* Strapping Pins = SP
ESP32 - S3 - WROOM1
Default Configuration of Strapping Pins Strapping Pin Default Configuration Bit Value GPIO0 Pull-up 1 GPIO3 Floating - GPIO45 Pull-down 0 GPIO46 Pull-down 0
JTAG mode
PUSH BUTTONS
GPIO0 has an internal pullup resistor, so if it is left unconnected then it will pull high.
ESD PROTECTION
Buttons for BOOT and ENABLE functions.
Typically these can be used, but you need to make sure they are not in the wrong state during boot. gpio.0 Boot Mode. Weak pullup during reset. (Boot Mode 0=Boot from Flash, 1=Download) gpio.3 JTAG Mode. Weak pull down during reset. (JTAG Config) gpio.45 SPI voltage. Weak pull down during reset. (S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
ESP32: Only pins that support both input & output have integrated pull-up and pull-down resistors. Input-only GPIOs 34-39 do not.
EN=RESET, BOOT=bootloader mode
Data transfer USB connector connected to ESP32 using CDC method
BOOT


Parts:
C10, C11, C12, C13: 10uF.stabl; C_1206_3216Metric_Pad1.33x1.80mm_HandSolder
IC1: XT30U-F; AMASS_XT30U-M_1x02_P5.0mm_Vertical; Manufacturer_Part_Number XT30U-M; LCSC C99101
U7: LM1084IS-5.0/NOPB; TO-252-3_TabPin2
U8: LM1084IS-3.3/NOPB; TO-252-3_TabPin2

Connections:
+3V3: C13.1, U8.2 (VO); also elsewhere on the board
+5V: C11.1, C12.1, U7.2 (VO), U8.3 (VI); also elsewhere on the board
+8V: C10.1, U7.3 (VI); also elsewhere on the board
GND: C10.2, C11.2, C12.2, C13.2, IC1.1, U7.1 (GND), U8.1 (GND); also elsewhere on the board
VBATT: IC1.2; also elsewhere on the board

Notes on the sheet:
Voltage stabilaser LM1084 Input voltage 8,4V Voltage regulator - 3,3V Output current - 5A
XT-30 Connector (male) Connector with 2mm bullets contacts for currents up to 30 A. Gold-plated contacts Non-interchangeable polarity. connected with XT-30 female type connector that is wired to the battery Battery specs: - 2S LiPo - 3.7V nominal voltage on one cell - 8,4 in total (4,2 fully charge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
STABILIZATOR
XT30M KONEKTOR


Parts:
J6, J7, J9: Conn_01x06_Pin; JST_SH_BM06B-SRSS-TB_1x06-1MP_P1.00mm_Vertical
J8: TSOP382xx; PinSocket_1x03_P2.54mm_Vertical
JP1: SolderJumper_3_Open; SolderJumper-3_P2.0mm_Open_TrianglePad1.0x1.5mm
R8, R9, R10, R11, R12, R13: 0R; R_1206_3216Metric
R14, R16, R18: 100; R_1206_3216Metric
R15, R17, R19: 10k; R_1206_3216Metric
U4, U5, U6: QRE1113; OnSemi_CASE100AQ - QRE1113

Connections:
+3V3: J8.3 (Vs), JP1.1 (A), R14.2, R15.1, R16.2, R17.1, R18.2, R19.1; also elsewhere on the board
+5V: JP1.3 (B); also elsewhere on the board
GND: J6.4, J7.4, J8.2 (GND), J9.4, R9.1, R11.1, R13.1, U4.2 (K), U4.4, U5.2 (K), U5.4, U6.2 (K), U6.4; also elsewhere on the board
IR MODULE: J8.1 (OUT); also elsewhere on the board
unnamed: J6.5, R8.1, R9.2
unnamed: J7.5, R10.1, R11.2
unnamed: J9.5, R12.1, R13.2
unnamed: R14.1, U4.1 (A)
unnamed: R16.1, U5.1 (A)
unnamed: R18.1, U6.1 (A)
QRE1113 B: R15.2, U4.3; also elsewhere on the board
QRE1113 C: R17.2, U5.3; also elsewhere on the board
QRE1113 D: R19.2, U6.3; also elsewhere on the board
SCL: J6.3, J7.3, J9.3; also elsewhere on the board
SDA: J6.2, J7.2, J9.2; also elsewhere on the board
SENSOR_SUPPLY: J6.1, J7.1, J9.1, JP1.2 (C)
X-SHUT1: R8.2; also elsewhere on the board
X-SHUT2: R10.2; also elsewhere on the board
X-SHUT3: R12.2; also elsewhere on the board

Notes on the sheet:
Time-of-Flight(ToF) laser-ranging module - TF-LC02 COMMUNICATION PROTOCOL: I²C
IR LED Reciver module Operating voltage: 2.7V to 5.5V Frequency: 38kHz High immunity against ambient light. For more than 1 input use - Hexadecimal code Used as a main program starter
INFRAČERVENÍ MODUL
SENZORY ČÁRÝ
When pin 5 is connected to ground, TF-Luna enters I2C mode, then its pin 2 is use as SDA data and pin 3 is the SCL clock sending data.
Miniature Reflective Object Sensor - QRE1113 IR reflectance sensor is comprised of two parts - an IR emitting LED and an IR sensitive phototransistor. Analog output A 100Ω resistor is placed in series with the LED to limit current. A 10kΩ resistor pulls the output pin high, but when the light from 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
TF-LUNA MANUAL
SENZORY VZDALENOSTI

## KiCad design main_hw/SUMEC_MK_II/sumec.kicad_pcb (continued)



Board: 2 copper layers, 92.0 x 56.5 mm, 59 parts (16 on the bottom side), 47 nets.

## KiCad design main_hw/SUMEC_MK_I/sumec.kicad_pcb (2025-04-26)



Board: 2 copper layers, 95.0 x 73.0 mm, 34 parts (4 on the bottom side), 33 nets.

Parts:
C1, C2: 10uF; CP_Radial_D4.0mm_P2.00mm
D1: RLED; LED_D5.0mm
D2: D_Schottky; D_A-405_P10.16mm_Horizontal
H1, H2, H3: MountingHole M3; MountingHole_3.2mm_M3
IC1: XT30U-F; AMASS_XT30U-M_1x02_P5.0mm_Vertical
J1, J2, J3, J4: Conn_01x01_Pin; SolderWire-0.5sqmm_1x01_D0.9mm_OD2.3mm
R1: 75; R_Axial_DIN0207_L6.3mm_D2.5mm_P10.16mm_Horizontal
R2, R4, R6, R8: 100; R_Axial_DIN0207_L6.3mm_D2.5mm_P10.16mm_Horizontal
R3, R5, R7, R9: 10k; R_Axial_DIN0207_L6.3mm_D2.5mm_P10.16mm_Horizontal
SW1: SW_SPDT; JST_EH_B3B-EH-A_1x03_P2.50mm_Vertical
SW3: SW_Push; SW_PUSH_6mm
U1: ESP32-DEVKIT-V1; MODULE_ESP32_DEVKIT_V1 B_Cu - PADS and no mount holes
U2, U3, U4: VL53L0X; GY-530 VL53L0X
U5: TSOP382xx; PinSocket_1x03_P2.54mm_Vertical
U6, U7, U8, U9: QRE1113; OnSemi_CASE100AQ - QRE1113
U10: LD1117AV33; TO-220-3_Vertical
U11: ROB-14450; ROB-14450 - TB6612FNG (MOTOR DRIVER)

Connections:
12V IN: IC1.2, SW1.1 (A)
+3V3: C1.1, R2.2, R3.1, R4.2, R5.1, R6.2, R7.1, R8.2, R9.1, SW3.1, U2.1 (VIN), U3.1 (VIN), U4.1 (VIN), U5.3 (Vs), U10.2 (OUT), U11.2 (VCC)
+12V: C2.1, D2.2 (A), SW1.2 (B), U10.3 (IN), U11.1 (VM)
AI1: U1.10 (D19), U11.14 (AI1)
AI2: U1.9 (D18), U11.15 (AI2)
BI1: U1.5 (D4), U11.12 (BI1)
BI2: U1.4 (D2), U11.11 (BI2)
GND: C1.2, C2.2, D1.1 (K), IC1.1, U1.2 (GND), U1.29 (GND), U2.2 (GND), U3.2 (GND), U4.2 (GND), U5.2 (GND), U6.2 (K), U6.4, U7.2 (K), U7.4, U8.2 (K), U8.4, U9.2 (K), U9.4, U10.1 (ADJ/GND), U11.3 (GND), U11.8 (GND), U11.9 (GND)
IR MODULE: U1.18 (GPIX39_VN), U5.1 (OUT)
LED SIGNALISATION: R1.2, U1.26 (D14)
MOTOR 1 +: J1.1, U11.4 (A01)
MOTOR 1 -: J2.1, U11.5 (A02)
MOTOR 2 +: J4.1, U11.6 (B02)
MOTOR 2 -: J3.1, U11.7 (B01)
unnamed: D1.2 (A), R1.1
unnamed: D2.1 (K), U1.30 (VIN)
unnamed: R2.1, U6.1 (A)
unnamed: R4.1, U7.1 (A)
unnamed: R6.1, U8.1 (A)
unnamed: R8.1, U9.1 (A)
PWMA: U1.8 (D5), U11.16 (PWMA)
PWMB: U1.3 (D15), U11.10 (PWMB)
QRE1113 A: R3.2, U1.20 (D35), U6.3
QRE1113 B: R5.2, U1.21 (D32), U7.3
QRE1113 C: R7.2, U1.19 (D34), U8.3
QRE1113 D: R9.2, U1.22 (D33), U9.3
SCL: U1.14 (D22_SCL), U2.3 (SCL), U3.3 (SCL), U4.3 (SCL)
SDA: U1.11 (D21_SDA), U2.4 (SDA), U3.4 (SDA), U4.4 (SDA)
STBY: U1.15 (D23), U11.13 (STBY)
TEST PROGRAM: SW3.2, U1.28 (D13)
X-SHUT 1: U1.25 (D27), U2.6 (XSHUT)
X-SHUT 2: U1.23 (D25), U3.6 (XSHUT)
X-SHUT 3: U1.24 (D26), U4.6 (XSHUT)

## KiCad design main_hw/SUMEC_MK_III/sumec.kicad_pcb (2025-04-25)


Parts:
R4: R; SPS LOGO
R12: R; VIGIL 2
R20: R; R2D2
R21: R; Logo


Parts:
H1, H2, H3: MountingHole_Pad; MountingHole_3.2mm_M3_Pad
J1: Conn_01x04_Pin; JST_XH_B4B-XH-A_1x04_P2.50mm_Vertical
J2: Conn_01x01_Pin; SolderWire-0.1sqmm_1x01_D0.4mm_OD1mm
SW1: SW_Push; SW_SPST_B3U-1000P
SW2: SW_DPDT_x2; Custom_SPDT_4.8mm_Switch

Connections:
+3V3: SW1.1; also elsewhere on the board
+12V: SW2.1 (A); also elsewhere on the board
GND: H1.1, H2.1, H3.1; also elsewhere on the board
OUT 1A: J1.2; also elsewhere on the board
OUT 1B: J1.1; also elsewhere on the board
OUT 2A: J1.4; also elsewhere on the board
OUT 2B: J1.3; also elsewhere on the board
TEST PROGRAM: SW1.2; also elsewhere on the board
VBATT: SW2.2 (B); also elsewhere on the board
VBUS 5V: J2.1; also elsewhere on the board

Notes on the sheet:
MOUNTING HOLES
Mounting holes M3 Mounting holes that are screwed to the threaded holes on the chassis.
MAIN SWITCH
TESTED - WORKS, INSPECTED
Motors
INSPECTED
TEST BUTTON
Main switch is at the top of the robot for ease of access
5V from USB
FOOTPRINT CREATED FROM 3D MODEL, INSPECTED
CONNECTORS
Tactile swicth (button) Used for starting test code program LED is used as indicator of starting the said program - (subjcet to change depending on different usage of LED, for example; multiple flashing for trouble-shooting or indicating)



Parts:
C1: 10uF.mcu; CP_EIA-3216-18_Kemet-A_Pad1.58x1.35mm_HandSolder
C2: 100nF.mcu; C_0805_2012Metric_Pad1.18x1.45mm_HandSolder
C3, C4: 22nF.hb; C_0805_2012Metric_Pad1.18x1.45mm_HandSolder
C5, C6, C13: 100nF; C_0805_2012Metric_Pad1.18x1.45mm_HandSolder
C7, C8: 100nF.hb; C_0805_2012Metric_Pad1.18x1.45mm_HandSolder
C9, C10: 10uF.hb; CP_EIA-3216-18_Kemet-A_Pad1.58x1.35mm_HandSolder
C11: 100nF.en; C_0805_2012Metric_Pad1.18x1.45mm_HandSolder
C12: 100nF.boot; C_0805_2012Metric_Pad1.18x1.45mm_HandSolder
D1, D2, D4: LED; LED_0805_2012Metric_Pad1.15x1.40mm_HandSolder
D3: D_Schottky; D_1206_3216Metric_Pad1.42x1.75mm_HandSolder
IC1, IC2: DRV8874PWPR; DRV8874; Manufacturer_Part_Number DRV8874PWPR; Mouser Part Number 595-DRV8874PWPR
J3: TYPE-C-31-M-12; USB_Type_C; PARTREV 2020.12.08
R1, R2: 100R; R_0805_2012Metric_Pad1.20x1.40mm_HandSolder
R3: 560R; R_0805_2012Metric_Pad1.20x1.40mm_HandSolder
R5: 0R; R_1206_3216Metric_Pad1.30x1.75mm_HandSolder
R6, R7: 15R; R_0805_2012Metric_Pad1.20x1.40mm_HandSolder
R8: 10k.mcu; R_0805_2012Metric_Pad1.20x1.40mm_HandSolder
SW3, SW4: SW_Push; SW_SPST_B3U-1000P
U1: ESP32-S3-WROOM-1
U2: USBLC6-2SC6; TSOT-23-6_HandSoldering

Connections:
+3V3: C1.1, C2.1, R8.2, U1.2 (3V3); also elsewhere on the board
+12V: C5.1, C6.1, C7.2, C8.2, C9.1, C10.1, D4.2 (A), IC1.11 (VM), IC2.11 (VM); also elsewhere on the board
BOOT: C12.1, SW4.2, U1.27 (GPIO0/BOOT)
D+: U1.14 (GPIO20/U1CTS/ADC2_CH9/CLK_OUT1/USB_D+), U2.6
D+ IN: J3.A6 (DP1), J3.B6 (DP2), R6.1
D-: U1.13 (GPIO19/U1RTS/ADC2_CH8/CLK_OUT2/USB_D-), U2.4
D- IN: J3.A7 (DN1), J3.B7 (DN2), R7.1
EN: C11.1, R8.1, SW3.2, U1.3 (EN)
GND: C1.2, C2.2, C7.1, C8.1, C9.2, C10.2, C11.2, C12.2, C13.2, IC1.9 (PGND), IC1.15 (GND), IC1.16 (PMODE), IC1.17 (EP), IC2.9 (PGND), IC2.15 (GND), IC2.16 (PMODE), IC2.17 (EP), J3.A1_B12 (GND), J3.B1_A12 (GND), R1.2, R2.2, R3.2, R5.2, SW3.1, SW4.1, U1.1 (GND), U1.40 (GND), U1.41 (GND), U2.2; also elsewhere on the board
IN1: IC1.2 (PH/IN2), U1.20 (GPIO12/TOUCH12/ADC2_CH1/FSPICLK/FSPIIO6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)
IN2: IC2.2 (PH/IN2), U1.21 (GPIO13/TOUCH13/ADC2_CH2/FSPIQ/FSPIIO7/S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)
IR MODULE: U1.31 (GPIO38/FSPIWP/SUBSPIWP); also elsewhere on the board
LED1: D1.2 (A), U1.24 (GPIO47/SPICLK_P/SUBSPICLK_P_DIFF)
LED2: D2.2 (A), U1.25 (GPIO48/SPICLK_N/SUBSPICLK_N_DIFF)
unnamed: D1.1 (K), R1.1
unnamed: D2.1 (K), R2.1
unnamed: D3.2 (A), J3.A4_B9 (VBUS), J3.B4_A9 (VBUS)
unnamed: D4.1 (K), R3.1
unnamed: C3.2, IC1.13 (CPH)
unnamed: C3.1, IC1.14 (CPL)
unnamed: C5.2, IC1.12 (VCP)
unnamed: C4.2, IC2.13 (CPH)
unnamed: C4.1, IC2.14 (CPL)
unnamed: C6.2, IC2.12 (VCP)
unnamed: J3.S1 (SHIELD), J3.S2 (SHIELD), J3.S3 (SHIELD), J3.S4 (SHIELD), R5.1
unnamed: R6.2, U2.1
unnamed: R7.2, U2.3
OUT 1A: IC1.8 (OUT1); also elsewhere on the board
OUT 1B: IC1.10 (OUT2); also elsewhere on the board
OUT 2A: IC2.8 (OUT1); also elsewhere on the board
OUT 2B: IC2.10 (OUT2); also elsewhere on the board
PWM1: IC1.1 (EN/IN1), U1.22 (GPIO14/TOUCH14/ADC2_CH3/FSPIWP/FSPIDQS/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)
PWM2: IC2.1 (EN/IN1), U1.23 (GPIO21)
QRE1113 A: U1.17 (GPIO9/TOUCH9/ADC1_CH8/FSPIHD/SUBSPIHD); also elsewhere on the board
QRE1113 B: U1.18 (GPIO10/TOUCH10/ADC1_CH9/FSPICS0/FSPIIO4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); also elsewhere on the board
QRE1113 C: U1.12 (GPIO8/TOUCH8/ADC1_CH7/SUBSPICS1); also elsewhere on the board
SCL: U1.10 (GPIO17/U1TXD/ADC2_CH6); also elsewhere on the board
SDA: U1.11 (GPIO18/U1RXD/ADC2_CH7/CLK_OUT3); also elsewhere on the board
SHARP 1: U1.9 (GPIO16/U0CTS/ADC2_CH5/XTAL_32K_N); also elsewhere on the board
SHARP 2: U1.28 (SPIIO6/GPIO35/FSPID/SUBSPID); also elsewhere on the board
TEST PROGRAM: U1.38 (GPIO2/TOUCH2/ADC1_CH1); also elsewhere on the board
VBUS 5V: C13.1, D3.1 (K), U2.5; also elsewhere on the board
nSLEEP: IC1.3 (NSLEEP), IC2.3 (NSLEEP), U1.19 (GPIO11/TOUCH11/ADC2_CH0/FSPID/FSPIIO5/S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)

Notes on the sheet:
ADC1
USB
I2C
0.1-µF bypass capacitor to ground, as well as sufficient Bulk Capacitance rated for VM
SPI voltage
Enable (EN) is the 3.3V regulator’s enable pin. It’s pulled up, so connect to ground to disable the 3.3V regulator. This means that you can use this pin connected to a pushbutton to restart your ESP32, for example.
USB CONNECTOR
Status LED2
Sleep mode input. Logic high to enable device. Logic low to enter low-power sleep mode.
USB Type-C Connector
GPIO0, GPIO45, and GPIO46 are connected to the chip's internal weak pull-up/pull-down resistors at chip reset. These resistors determine the default bit values of the strapping pins. Also, these resistors determine the bit values if the strapping pins are connected to an external high-impedance cir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
E-Pad
Overcurrent protection - Current regulation
ENABLE
Analog current output propotaional to load current.
GPIO USB 20 D+ (green) 19 D- (white) GND GND (black) NC +5V (red)
H-BRIDGE / DRIVER
Status LED1
H-bridge control input mode.
PINOUT INPSECTED
BOOT mode
If the device does not support the auto download mode, you need to get into the download mode manually. To do so, press and hold the BOOT button and then press the RESET button once. After that release the BOOT button.
* Strapping Pins = SP
Battery power
ESP32 - S3 - WROOM1
Default Configuration of Strapping Pins Strapping Pin Default Configuration Bit Value GPIO0 Pull-up 1 GPIO3 Floating - GPIO45 Pull-down 0 GPIO46 Pull-down 0
JTAG mode
PUSH BUTTONS
GPIO0 has an internal pullup resistor, so if it is left unconnected then it will pull high.
TESTED - WORKS, INSPECTED
ESD PROTECTION
Buttons for BOOT and ENABLE functions.
Typically these can be used, but you need to make sure they are not in the wrong state during boot. gpio.0 Boot Mode. Weak pullup during reset. (Boot Mode 0=Boot from Flash, 1=Download) gpio.3 JTAG Mode. Weak pull down during reset. (JTAG Config) gpio.45 SPI voltage. Weak pull down during reset. (S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
ESP32: Only pins that support both input & output have integrated pull-up and pull-down resistors. Input-only GPIOs 34-39 do not.
INPSECTED
ESP32-S3 Datasheet
EN=RESET, BOOT=bootloader mode
Data transfer USB connector connected to ESP32 using CDC method
BOOT
(nFault)Fault indicator output. Pulled low during a fault condition. Connect an external pullup resistor for open-drain operation.


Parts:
C16, C17, C18, C19: 10uF.stabl; CP_EIA-3216-18_Kemet-A_Pad1.58x1.35mm_HandSolder
J11: XT30PW-M; AMASS_XT30PW-M; PARTREV 1.2
U4: LM1084-5.0; TO-263-3_TabPin2
U5: LM1084-3.3; TO-263-3_TabPin2

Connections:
+3V3: C19.1, U5.2 (VO); also elsewhere on the board
+5V: C17.1, C18.1, U4.2 (VO), U5.3 (VI); also elsewhere on the board
+12V: C16.1, U4.3 (VI); also elsewhere on the board
GND: C16.2, C17.2, C18.2, C19.2, J11.N, U4.1 (GND), U5.1 (GND); also elsewhere on the board
VBATT: J11.P; also elsewhere on the board

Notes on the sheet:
Texas Instruments 2 LDO Voltage Regulators 5A - 3.3V and 5V. LM1084IS-5.0/NOPB 5V LM1084IS-3.3/NOPB 3.3V Using TO-263-3 footprint
TESTED - WORKS, INSPECTED
XT-30 Connector (male) Connector with 2mm bullets contacts for currents up to 30 A. Gold-plated contacts Non-interchangeable polarity. connected with XT-30 female type connector that is wired to the battery Battery specs: - 2S LiPo - 3.7V nominal voltage on one cell - 8,4 in total (4,2 fully charge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
STABILISER
XT30M CONNECTOR

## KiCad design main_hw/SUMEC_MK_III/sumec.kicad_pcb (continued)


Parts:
C14, C15: 10uF.shrp; CP_EIA-3216-18_Kemet-A_Pad1.58x1.35mm_HandSolder
J4, J5, J6: Conn_01x06_Pin; Molex_PicoBlade_53398-0671_1x06-1MP_P1.25mm_Vertical
J7, J8, J10: Conn_01x03_Pin; Molex_PicoBlade_53398-0371_1x03-1MP_P1.25mm_Vertical
J9: Conn_01x04_Pin; Molex_PicoBlade_53398-0471_1x04-1MP_P1.25mm_Vertical
R9: 10k; R_0805_2012Metric_Pad1.20x1.40mm_HandSolder
R10: 100; R_0805_2012Metric_Pad1.20x1.40mm_HandSolder
U3: TSOP382xx; TSOP

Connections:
+3V3: C14.1, C15.1, J7.2, J8.2, J9.3, R9.1, R10.1, U3.3 (Vs); also elsewhere on the board
+5V: J4.1, J5.1, J6.1; also elsewhere on the board
GND: C14.2, C15.2, J4.4, J4.5, J5.4, J5.5, J6.4, J6.5, J7.3, J8.3, J9.2, J10.3, U3.2 (GND); also elsewhere on the board
IR MODULE: U3.1 (OUT); also elsewhere on the board
unnamed: J10.2, R10.2
QRE1113 A: J9.1; also elsewhere on the board
QRE1113 B: J9.4; also elsewhere on the board
QRE1113 C: J10.1, R9.2; also elsewhere on the board
SCL: J4.3, J5.3, J6.3; also elsewhere on the board
SDA: J4.2, J5.2, J6.2; also elsewhere on the board
SHARP 1: J7.1; also elsewhere on the board
SHARP 2: J8.1; also elsewhere on the board

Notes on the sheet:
Time-of-Flight(ToF) laser-ranging module - TF-Luna COMMUNICATION PROTOCOL: I²C
conn molex 4pin picoblade pro zadni QRE, 2 conn 1. pro predni board, a 2. pro samostatni qre.
IR LED Reciver module Operating voltage: 2.7V to 5.5V Frequency: 38kHz High immunity against ambient light. For more than 1 input use - Hexadecimal code Used as a main program starter
Digital distance sensor - Sharp GP2Y0D810Z0F
TESTED - WORKS, INSPECTED
IR MODULE
INSPECTED
SENZORY ČÁRY
When pin 5 is connected to ground, TF-Luna enters I2C mode, then its pin 2 is used as SDA data and pin 3 is the SCL clock sending data. Addresses are saved using Nat Simak's program.
Sensor detects objects between 2 cm and 10 cm Low when detecting an object, high otherwise. Frequency - 390 Hz Operating voltage 2.7V - 6.2V
Miniature Reflective Object Sensor - QRE1113 IR reflectance sensor is comprised of two parts - an IR emitting LED and an IR sensitive phototransistor. Analog output A 100Ω resistor is placed in series with the LED to limit current. A 10kΩ resistor pulls the output pin high, but when the light from 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
TF-LUNA MANUAL
DISTANCE SENSORS
MIRRORED
DISTANCE SENSORS - SIDE



Board: 2 copper layers, 95.0 x 55.0 mm, 61 parts (19 on the bottom side), 46 nets.

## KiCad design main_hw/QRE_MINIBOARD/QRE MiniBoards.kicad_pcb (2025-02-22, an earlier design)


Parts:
H1, H2: M3; MountingHole_3.2mm_M3_Pad
J2: Conn_01x04_Pin; Molex_PicoBlade_53261-0471_1x04-1MP_P1.25mm_Horizontal
R1, R3: 100; R_0805_2012Metric_Pad1.20x1.40mm_HandSolder
R2, R4: 10k; R_0805_2012Metric_Pad1.20x1.40mm_HandSolder
U1, U2: QRE1113; OnSemi_CASE100AQ - QRE1113

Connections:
+3V3: J2.2, R1.2, R2.1, R3.2, R4.1
GND: H1.1, H2.1, J2.3, U1.2 (K), U1.4, U2.2 (K), U2.4
unnamed: R1.1, U1.1 (A)
unnamed: R3.1, U2.1 (A)
QRE1113 A: J2.4, R2.2, U1.3
QRE1113 B: J2.1, R4.2, U2.3

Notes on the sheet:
QRE1113 Sensors
Horizontal PicoBlade 4pin connector
MECHANICAL



Board: 2 copper layers, 90.0 x 11.0 mm, 9 parts (2 on the bottom side), 6 nets.

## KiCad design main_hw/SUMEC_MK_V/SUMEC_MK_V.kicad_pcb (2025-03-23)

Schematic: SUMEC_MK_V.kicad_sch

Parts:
TP1, TP2, TP3, TP4, TP5, TP6: TestPoint

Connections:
unnamed: TP1.1, TP2.1, TP3.1, TP4.1, TP5.1, TP6.1

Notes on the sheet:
SUMEC LINKTREE
GRAPHICS
ULTRAKILL V1
1. Q: 2. Q: 3. Q: Left/right silk for sensors and motors 4. Q: 5. Q: Add IO pin numbers after the routing is done 6. Q: Does the voltage read need to be after the switch or before? 7. Q:
SPS LOGO
*The unit price is set for an order quantity of 10 units
SUMEC LOGO
ME FR
FREEFALL PANEL

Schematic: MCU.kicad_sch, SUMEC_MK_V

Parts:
C24, C26: 100nF; C_0805_2012Metric_Pad1.18x1.45mm_HandSolder
C25: 10uF; CP_EIA-3216-18_Kemet-A_Pad1.58x1.35mm_HandSolder
R36, R37: 10k; R_0805_2012Metric_Pad1.20x1.40mm_HandSolder
U4: 24CW1280T-I/OT; SOT-23-5
U5: ESP32-S3-WROOM-1

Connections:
+3V3: C24.1, C25.1, C26.1, R36.2, R37.2, U4.4 (V_{CC}), U5.2 (3V3); also elsewhere on the board
ACC_INT: U5.32 (IO39); also elsewhere on the board
BOOT: U5.27 (IO0); also elsewhere on the board
BTN_IOXX: U5.4 (IO4); also elsewhere on the board
BTN_IOXY: U5.5 (IO5); also elsewhere on the board
D+: U5.14 (IO20); also elsewhere on the board
D-: U5.13 (IO19); also elsewhere on the board
EN: U5.3 (EN); also elsewhere on the board
EN_L: U5.12 (IO8); also elsewhere on the board
EN_R: U5.7 (IO7); also elsewhere on the board
GND: C24.2, C25.2, C26.2, U4.2 (V_{SS}), U5.1 (GND), U5.40 (GND), U5.41 (GND); also elsewhere on the board
GYR_INT: U5.33 (IO40); also elsewhere on the board
IR_MODULE: U5.34 (IO41); also elsewhere on the board
LED_1: U5.37 (IO47); also elsewhere on the board
LED_2: U5.38 (IO2); also elsewhere on the board
LED_3: U5.39 (IO1); also elsewhere on the board
PH_L: U5.11 (IO18); also elsewhere on the board
PH_R: U5.6 (IO6); also elsewhere on the board
POL_M: U5.19 (IO11); also elsewhere on the board
POL_R: U5.20 (IO12); also elsewhere on the board
QRE_BACK: U5.9 (IO16); also elsewhere on the board
QRE_L: U5.22 (IO14); also elsewhere on the board
QRE_R: U5.21 (IO13); also elsewhere on the board
SCL: R37.1, U4.1 (SCL), U5.35 (IO42); also elsewhere on the board
SDA: R36.1, U4.3 (SDA), U5.36 (IO44); also elsewhere on the board
SHARP_L: U5.18 (IO10); also elsewhere on the board
SHARP_R: U5.31 (IO38); also elsewhere on the board
VOLTAGE_ALERT: U5.17 (IO9); also elsewhere on the board
nFAULT: U5.8 (IO15); also elsewhere on the board
nSLEEP: U5.10 (IO17); also elsewhere on the board

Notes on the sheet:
Typically these can be used, but you need to make sure they are not in the wrong state during boot. gpio.0 Boot Mode. Weak pullup during reset. (Boot Mode 0=Boot from Flash, 1=Download) gpio.3 JTAG Mode. Weak pull down during reset. (JTAG Config) gpio.45 SPI voltage. Weak pull down during reset. (S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
GPIO0 has an internal pullup resistor, so if it is left unconnected then it will pull high.
GPIO | NAME | DESC. 02 | MAIN_BTN | Schrack light switch; --debounced --pullup 05 | R_LED | LEDs, Indication --debug 06 | G_LED | LEDs, Indication --debug 09 | BUZZER | Passive buzzer 10 | MISO | SPI; SD Card 11 | CLOCK | SPI clock; SD Card, MAX7219 12 | MOSI | SPI; SD Card, MAX7219 04 | cSelect0 |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
ESP32-S3-WROOM1-N4
I2C Addr.: 0x50
GPIO0, GPIO45, and GPIO46 are connected to the chip's internal weak pull-up/pull-down resistors at chip reset. These resistors determine the default bit values of the strapping pins. Also, these resistors determine the bit values if the strapping pins are connected to an external high-impedance cir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
CHANGE LABELS
I2C bus is pullled up internally by esp32
ESP32-S3 Datasheet
INPUT_PULLUP
EEPROM
Default Configuration of Strapping Pins Strapping Pin Default Configuration Bit Value GPIO0 Pull-up 1 GPIO3 Floating - GPIO45 Pull-down 0 GPIO46 Pull-down 0

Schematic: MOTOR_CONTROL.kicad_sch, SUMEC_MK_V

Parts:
C16, C18: 22nF; C_0805_2012Metric_Pad1.18x1.45mm_HandSolder
C17, C19, C20, C21: 100nF; C_0805_2012Metric_Pad1.18x1.45mm_HandSolder
C22, C23: 10uF; CP_EIA-3216-18_Kemet-A_Pad1.58x1.35mm_HandSolder
IC2, IC3: DRV8874PWPR; DRV8874; Manufacturer_Part_Number DRV8874PWPR; Mouser Part Number 595-DRV8874PWPR
J2, J3: Conn_01x06_Socket; JST_SH_BM06B-SRSS-TB_1x06-1MP_P1.00mm_Vertical
JP2, JP3: SolderJumper_3_Open; SolderJumper-3_P2.0mm_Open_TrianglePad1.0x1.5mm
R15, R18: 0R/R-Ipropi; R_0805_2012Metric_Pad1.20x1.40mm_HandSolder
R16, R19: 0R/R-Imode; R_0805_2012Metric_Pad1.20x1.40mm_HandSolder
R17: 10k; R_0805_2012Metric_Pad1.20x1.40mm_HandSolder

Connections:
+3V3: IC2.5 (VREF), IC3.5 (VREF), J2.4, J3.4, JP2.1 (A), JP3.1 (A), R17.2; also elsewhere on the board
+12V: C17.2, C19.2, C20.2, C21.2, C22.1, C23.1, IC2.11 (VM), IC3.11 (VM); also elsewhere on the board
EN_L: IC3.1 (EN/IN1); also elsewhere on the board
EN_R: IC2.1 (EN/IN1); also elsewhere on the board
GND: C20.1, C21.1, C22.2, C23.2, IC2.9 (PGND), IC2.15 (GND), IC2.17 (EP), IC3.9 (PGND), IC3.15 (GND), IC3.17 (EP), J2.1, J3.1, JP2.3 (B), JP3.3 (B), R15.1, R16.1, R18.1, R19.1; also elsewhere on the board
MOTOR_L_1: IC3.8 (OUT1), J3.6
MOTOR_L_2: IC3.10 (OUT2), J3.5
MOTOR_R_1: IC2.8 (OUT1), J2.6
MOTOR_R_2: IC2.10 (OUT2), J2.5
unnamed: C16.2, IC2.13 (CPH)
unnamed: C16.1, IC2.14 (CPL)
unnamed: IC2.7 (IMODE), R16.2
unnamed: IC2.6 (IPROPI), R15.2
unnamed: C17.1, IC2.12 (VCP)
unnamed: C18.2, IC3.13 (CPH)
unnamed: C18.1, IC3.14 (CPL)
unnamed: IC3.7 (IMODE), R19.2
unnamed: IC3.6 (IPROPI), R18.2
unnamed: C19.1, IC3.12 (VCP)
OUT_L_A: J3.3
OUT_L_B: J3.2
OUT_R_A: J2.3
OUT_R_B: J2.2
PH_L: IC3.2 (PH/IN2); also elsewhere on the board
PH_R: IC2.2 (PH/IN2); also elsewhere on the board
PMODE_1: IC2.16 (PMODE), JP2.2 (C)
PMODE_2: IC3.16 (PMODE), JP3.2 (C)
nFAULT: IC2.4 (NFAULT), IC3.4 (NFAULT), R17.1; also elsewhere on the board
nSLEEP: IC2.3 (NSLEEP), IC3.3 (NSLEEP); also elsewhere on the board

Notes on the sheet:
CHANGE MOTORS TO DFFERENT CONNCETORS
PREF. 0R
CONTROL MODES: PMODE HIGH = PWM PMODE LOW = PH/EN
The internal current regulation can be disabled by tying IPROPI to GND and setting the VREF pin voltage greater than GND
EN-IN1
DRV8874 - Motor driver, H-Bridge Recommended Operating Conditions VM = 4.5V - 37V VM VIN = 0V - 5v I/PMODE, nSlEEP, EN/IN1, PH/IN2 fPWM = 0Hz - 100kHz EN/IN1, PH/IN2 Vref = 0V - 3.6V VREF Block Diagram:
ITRIP (A) x AIPROPI (μA/A) = VVREF (V) / RIPROPI (Ω)
H-BRIDGE
6-PIN JST SH-Style male connector VCC 2.7 V to 18 V encoder operating voltage
MOTORS
MOTOR - LEFT
MOTOR - RIGHT
PH-IN2

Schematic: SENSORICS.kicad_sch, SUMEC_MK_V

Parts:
C31, C33: 10uF; CP_EIA-3216-18_Kemet-A_Pad1.58x1.35mm_HandSolder
C32, C34: 100nF; C_0805_2012Metric_Pad1.18x1.45mm_HandSolder
J5: Conn_01x04_Pin; Molex_PicoBlade_53398-0471_1x04-1MP_P1.25mm_Vertical
J6: Conn_01x06_Pin; Molex_PicoBlade_53398-0671_1x06-1MP_P1.25mm_Vertical
J8, J10, J11, J12, J14, J15: Conn_01x03_Pin; Molex_PicoBlade_53398-0371_1x03-1MP_P1.25mm_Vertical
J13: Conn_01x03_Pin; PinHeader_1x03_P2.54mm_Vertical
R34: 10k; R_0805_2012Metric_Pad1.20x1.40mm_HandSolder
R35: 100R; R_0805_2012Metric_Pad1.20x1.40mm_HandSolder
U7: BMI088; PQFN50P450X300X100-16N

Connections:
+3V3: C31.1, C32.2, C33.1, C34.2, J5.3, J10.2, J11.2, J12.2, J13.3, J14.2, J15.2, R34.1, R35.1, U7.3 (VDD), U7.7 (PS), U7.10 (SDO2), U7.11 (VDDIO), U7.14 (CSB1), U7.15 (SDO1); also elsewhere on the board
+5V: J6.1; also elsewhere on the board
ACC_INT: U7.16 (INT1); also elsewhere on the board
GND: C31.2, C32.1, C33.2, C34.1, J5.2, J6.4, J6.5, J8.3, J10.3, J11.3, J12.3, J13.2, J14.3, J15.3, U7.4 (GNDA), U7.6 (GNDIO); also elsewhere on the board
GYR_INT: U7.12 (INT3); also elsewhere on the board
IR_MODULE: J13.1; also elsewhere on the board
unnamed: J8.2, R35.2
POL_L: J12.1
POL_M: J11.1; also elsewhere on the board
POL_R: J10.1; also elsewhere on the board
QRE_BACK: J8.1, R34.2; also elsewhere on the board
QRE_L: J5.4; also elsewhere on the board
QRE_R: J5.1; also elsewhere on the board
SCL: J6.3, U7.8 (SCL/SCK); also elsewhere on the board
SDA: J6.2, U7.9 (SDA/SDI); also elsewhere on the board
SHARP_L: J14.1; also elsewhere on the board
SHARP_R: J15.1; also elsewhere on the board

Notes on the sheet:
IR MODULE
( Better manual in -DOCS- )
IR LED Reciver module Operating voltage: 2.7V to 5.5V Frequency: 38kHz
Time-of-Flight(ToF) laser-ranging module - TF-Luna COMMUNICATION PROTOCOL: I²C When pin 5 is connected to ground, TF-Luna enters I2C mode, then its pin 2 is used as SDA data and pin 3 is the SCL clock sending data.
Digital distance sensor - Sharp GP2Y0D810Z0F Sensor detects objects between 2 cm and 10 cm Low when detecting an object, high otherwise. Operating voltage 2.7V - 6.2V
SIDE SENSORS
Pololu Distance Sensor with Pulse Width Output/Digital Output Small lidar based sensor can report presnece/distance of objects up to (TOTAL MAX 200cm-Digital, 300cm - PWM) Distance is chosen by configurating the jumpers with 0R resistors
POLOLU SENSOR MANUAL
TF-LUNA MANUAL
Digital distance sensor - Sharp GP2Y0D810Z0F Sensor detects objects between 2 cm and 10 cm Low when detecting an object, high otherwise. Frequency - 390 Hz Operating voltage 2.7V - 6.2V
IR LED Reciver module Operating voltage: 2.7V to 5.5V Frequency: 38kHz High immunity against ambient light. For more than 1 input use - Hexadecimal code Used as a main program starter
OBJECT DETECTING SENSORS
MIRRORED
DISTANCE MEASURING
SDO pins are I2C adress setting pins, when pulled high: ACCELEROMETER: 0x19 GYROSCOPE: 0x69
INERTIAL MEASURMENT UNIT
LINE SENSORS
Miniature Reflective Object Sensor - QRE1113

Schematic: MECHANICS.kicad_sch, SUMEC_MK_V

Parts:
C29, C30: 100nF; C_0805_2012Metric_Pad1.18x1.45mm_HandSolder
H1, H4: Mounting Hole M3; MountingHole_3.2mm_M3_Pad_Via
R33: 10k; R_0805_2012Metric_Pad1.20x1.40mm_HandSolder
SW2, SW3, SW4, SW5: SW_Push; SW_SPST_EVQPE1
TP7, TP8, TP9, TP10, TP11: TestPoint; TestPoint_Pad_1.0x1.0mm

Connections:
+3V3: R33.2, TP8.1; also elsewhere on the board
+5V: TP7.1; also elsewhere on the board
BOOT: C30.1, SW5.2; also elsewhere on the board
BTN_IOXX: SW3.2; also elsewhere on the board
BTN_IOXY: SW4.2; also elsewhere on the board
EN: C29.1, R33.1, SW2.2; also elsewhere on the board
GND: C29.2, C30.2, H1.1, H4.1, SW2.1, SW3.1, SW4.1, SW5.1; also elsewhere on the board
IR_MODULE: TP11.1; also elsewhere on the board
OUT 2A: TP9.1
OUT 2B: TP10.1

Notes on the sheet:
Buttons for BOOT and ENABLE functions. If the device does not support the auto download mode, you need to get into the download mode manually. To do so, press and hold the BOOT button and then press the RESET button once. After that release the BOOT button.
M3 Padded Mounting holes
ENABLE RESET
EN=reset, BOOT=bootloader mode Enable (EN) is the 3.3V regulator's enable pin. It's pulled up, so connect to ground to disable the 3.3V regulator. This means that you can use this pin connected to a pushbutton to restart your ESP32, for example.
BOOT
TESTING POINTS
PUSH BUTTONS
MOUNTING HOLES

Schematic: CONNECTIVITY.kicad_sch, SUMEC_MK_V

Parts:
BZ1: Buzzer; BUZZER_CUI_CPT
C27, C28: 100nF; C_0805_2012Metric_Pad1.18x1.45mm_HandSolder
D3, D4, D5, D6, D7: LED; LED_0805_2012Metric_Pad1.15x1.40mm_HandSolder
F1: Polyfuse/50R; Fuse_0805_2012Metric
J4: USB_TypeC; HRO_TYPE-C-31-M-12; PARTREV 2020.12.08
R24: 100k; R_0805_2012Metric_Pad1.20x1.40mm_HandSolder
R25, R26: 15R; R_0805_2012Metric_Pad1.20x1.40mm_HandSolder
R27: 0R; R_0805_2012Metric_Pad1.20x1.40mm_HandSolder
R28: 1k; R_0805_2012Metric_Pad1.20x1.40mm_HandSolder
R29, R30, R31, R32: 220R; R_0805_2012Metric_Pad1.20x1.40mm_HandSolder
U6: USBLC6-2SC6; TSOT-23-6_HandSoldering

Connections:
+12V: R28.1; also elsewhere on the board
/CONNECTIVITY/SHLD: C27.2, J4.S1 (SHIELD), J4.S2 (SHIELD), J4.S3 (SHIELD), J4.S4 (SHIELD), R24.1
BZ1_PWM: R27.1
D+: U6.4; also elsewhere on the board
D-: U6.6; also elsewhere on the board
D_NEG_IN: J4.A7 (DN1), J4.B7 (DN2), R25.1
D_POS_IN: J4.A6 (DP1), J4.B6 (DP2), R26.1
GND: BZ1.2 (-), C27.1, C28.2, D3.1 (K), D4.1 (K), D5.1 (K), D6.1 (K), D7.1 (K), J4.A1_B12 (GND), J4.B1_A12 (GND), R24.2, U6.2; also elsewhere on the board
LED_1: R30.1; also elsewhere on the board
LED_2: R31.1; also elsewhere on the board
LED_3: R32.1; also elsewhere on the board
unnamed: BZ1.1 (+), R27.2
unnamed: D3.2 (A), R28.2
unnamed: D4.2 (A), R29.2
unnamed: D5.2 (A), R30.2
unnamed: D6.2 (A), R31.2
unnamed: D7.2 (A), R32.2
unnamed: F1.2, J4.A4_B9 (VBUS), J4.B4_A9 (VBUS)
unnamed: R25.2, U6.1
unnamed: R26.2, U6.3
VBUS_USB: C28.1, F1.1, R29.1, U6.5; also elsewhere on the board

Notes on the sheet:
VBUS Power
BUZZER
GPIO USB 20 D+ (green) 19 D- (white) GND GND (black) VBUS +5V (red)
Status LED2
LED SIGNALISATION
Battery power
Status LED1
USB
USB Type-C Connector Data transfer USB connector connected to ESP32 using CDC method
ESD PROTECTION
Status LED3
USB CONNECTOR

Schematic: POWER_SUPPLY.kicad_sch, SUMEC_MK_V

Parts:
C1, C13, C35: 100nF; C_0805_2012Metric_Pad1.18x1.45mm_HandSolder
C3, C7, C8, C9, C14, C15: 22uF; CP_EIA-2012-12_Kemet-R_Pad1.30x1.05mm_HandSolder
C5, C11: 100nF; C_0805_2012Metric_Pad1.18x1.45mm_HandSolder; LCSC C49678
C12: 10uF; CP_EIA-3216-18_Kemet-A_Pad1.58x1.35mm_HandSolder
D1, D2: D_Schottky; D_1206_3216Metric_Pad1.42x1.75mm_HandSolder
IC1: TPS565242DRLR; SOT-563; Manufacturer_Part_Number TPS565242DRLR; Mouser Part Number 595-TPS565242DRLR
J1: XT30PW-M; PARTREV 1.2
JP1: SolderJumper_3_Open; SolderJumper-3_P2.0mm_Open_TrianglePad1.0x1.5mm
L1: 1.5uH; L_Vishay_IHLP-1212
L3: 3.3uH; L_Vishay_IHLP-1616
Q1, Q2: Q_PMOS; SOT-23-3
R3, R5, R6, R11, R13: 10k; R_0805_2012Metric_Pad1.20x1.40mm_HandSolder
R4: 2m; R_0805_2012Metric_Pad1.20x1.40mm_HandSolder
R7: 45k; R_0805_2012Metric_Pad1.20x1.40mm_HandSolder; LCSC C17470
R8: 10k; R_0805_2012Metric_Pad1.20x1.40mm_HandSolder; LCSC C17633
R10: 15k; R_0805_2012Metric_Pad1.20x1.40mm_HandSolder
R12: 52.3k; R_0805_2012Metric_Pad1.20x1.40mm_HandSolder
SW1: SW_DPDT_x2; Custom_SPDT_2.5_Switch
U1: INA226; VSSOP-10_3x3mm_P0.5mm
U3: AP62301Z6; SOT-563

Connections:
+3V3: C1.2, C7.1, C8.1, C9.1, C11.1, L1.2, R3.1, R7.1, U1.6 (VS); also elsewhere on the board
+5V: C3.1, C5.1, C35.1, D1.1 (K), D2.1 (K), IC1.1 (VIN), IC1.5 (EN); also elsewhere on the board
+12V: C12.1, Q2.3 (D), R10.1, U3.3 (IN); also elsewhere on the board
/POWER/FB_5V: R12.2, R13.1, U3.4 (FB)
/POWER/FET_SW: Q2.1 (G), R6.2, SW1.1 (A)
/POWER/SW: C13.1, L3.1, U3.2 (SW)
FB: IC1.6 (FB), R7.2, R8.1
GND: C1.1, C3.2, C5.2, C7.2, C8.2, C9.2, C11.2, C12.2, C14.2, C15.2, C35.2, IC1.3 (GND), IC1.4 (AGND), J1.N, R5.2, R8.2, R11.2, R13.2, SW1.2 (B), U1.1 (A1), U1.2 (A0), U1.7 (GND), U3.1 (GND); also elsewhere on the board
unnamed: D1.2 (A), Q1.3 (D)
unnamed: IC1.2 (SW), L1.1
unnamed: C13.2, U3.6 (BST)
unnamed: R10.2, R11.1, U3.5 (EN)
SCL: U1.5 (SCL); also elsewhere on the board
SDA: U1.4 (SDA); also elsewhere on the board
VBATT: J1.P, JP1.3 (B), R4.1, U1.10 (Vin+)
VBATT_SHUNT: JP1.1 (A), Q2.2 (S), R4.2, R6.1, U1.9 (Vin-)
VBUS_INA226: JP1.2 (C), U1.8 (Vbus)
VBUS_USB: D2.2 (A), Q1.1 (G), R5.1; also elsewhere on the board
VOLTAGE_ALERT: R3.2, U1.3 (~Alert); also elsewhere on the board
VOUT_5V: C14.1, C15.1, L3.2, Q1.2 (S), R12.1

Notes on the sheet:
SWITCHING SIMULATION - FALSTAD
TPS62133 Step down converter Input: 3-17V Output: 5V Current output: 3A Switching freq.: 2.5MHz Inductor Inductance: 2.2uH Max. current: 4.7A
BATTERY
USB POWER SWITCH
Power switching between 5V VBUS - USB and 5V Buck converter - BATT
MAIN SWITCH
I2C adress = 0x40
STEPDOWN CONVERTER 3.3V
STEPDOWN CONVERTER 5V
VOLTAGE READING
Rds On = 22.7 mOhms Vds = 30 V Vgs = - 20 V, + 16 V Vgs th = 2.2 V
- 2S/3S LiPo - 3.7V Cell voltage (nominal voltage) - 4,2V Cell voltage (fully charged) - 400mAh (may vary)
TPS62133 Step down converter Input: 3-17V Output: 5V Current output: 3A Switching freq.: 2.5MHz Inductor Inductance: 2.2uH Max. current: 3.8A
4A?
FeedBack voltage divider, usinf formula from datasheet 45.3 in reality? check before ordering.
will 0805 resistor be sufficent?
EN max voltage = 6V... "Leave floating for automatic startup"



Board: 4 copper layers, 97.0 x 37.5 mm, 110 parts (52 on the bottom side), 74 nets.

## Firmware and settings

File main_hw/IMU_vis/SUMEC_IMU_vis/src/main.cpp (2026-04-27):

#include <Arduino.h>
#include <Wire.h>
#include <Adafruit_Sensor.h>
#include <Adafruit_BNO055.h>
#include <utility/imumaths.h>

#define SDA_PIN 36
#define SCL_PIN 35

Adafruit_BNO055 bno = Adafruit_BNO055(55, 0x29, &Wire); 

void setup() {
  Serial.begin(115200);
  Wire.begin(SDA_PIN, SCL_PIN, 100000); 
  delay(500); 

  if (!bno.begin()) {
    Serial.println("BNO055 not found!");
    while (1);
  }
}

void loop() {
  // Get Quaternions directly from the sensor hardware
  imu::Quaternion quat = bno.getQuat();
  
  // Print in the format expected by the Python parser
  Serial.print("Quat: ");
  Serial.print(quat.w(), 4);
  Serial.print(", ");
  Serial.print(quat.x(), 4);
  Serial.print(", ");
  Serial.print(quat.y(), 4);
  Serial.print(", ");
  Serial.println(quat.z(), 4);

  delay(20); 
}

//cd C:\Users\MenMe\Documents\GitHub\GPS-Compass\_code\Python_IMU_viz
//cd C:\Users\MenMe\GitHub\GPS-Compass\_code\IMU_vis
//cd C:\Users\MenMe\GitHub\GPS-Compass\_code\IMU_vis\Python_IMU_vis

//cd C:\Users\MenMe\Documents\GitHub\Sumec-MiniSumo-HW\main_hw\IMU_vis\Python_IMU_vis

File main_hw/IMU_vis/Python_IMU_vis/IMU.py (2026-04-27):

import serial
import os
import sys
import time
import numpy as np
from scipy.spatial.transform import Rotation as R_sci
from vedo import Mesh, Plotter, Text2D

# --- CONFIG ---
SERIAL_PORT = 'COM3' 
BAUD_RATE = 115200
FILENAME = "SUMEC_Mk5_Pro.stl"
BASE_PATH = os.path.dirname(os.path.abspath(__file__))
MODEL_PATH = os.path.join(BASE_PATH, FILENAME)
UPDATE_INTERVAL = 0.05

# --- GLOBALS ---
quat_offset = R_sci.from_quat([0.0, 0.0, 0.0, 1.0]) 
current_quat = R_sci.from_quat([0.0, 0.0, 0.0, 1.0])
last_update = 0.0

# --- SERIAL SETUP ---
try:
    ser = serial.Serial(SERIAL_PORT, BAUD_RATE, timeout=0.1)
    ser.setDTR(True)
    ser.setRTS(True)
except Exception as e:
    print(f"Serial Error: {e}")
    sys.exit()

# --- VEDO SETUP ---
plt = Plotter(axes=1, bg='white', size=(1000, 700), interactive=False)

if not os.path.exists(MODEL_PATH):
    print(f"ERROR: {FILENAME} not found at {MODEL_PATH}")
    sys.exit()

model = Mesh(MODEL_PATH).c('gold')
original_pts = model.vertices.copy()

try:
    model.add_shadow()
except Exception:
    pass

msg = Text2D("Initializing...", pos='top-left', c='black', font='VictorMono')

# --- KEYBOARD CALLBACK ---
def on_key(event):
    global quat_offset, current_quat
    if event.keypress in ('z', 'Z'):
        quat_offset = current_quat
        print("\n>>> SENSOR ZEROED <<<\n")

# --- TIMER CALLBACK ---
def loop_func(event):
    global current_quat, last_update

    now = time.time()
    latest_line = None
    
    try:
        while ser.in_waiting > 0:
            line = ser.readline().decode('ascii', errors='ignore').strip()
            if "Quat:" in line:
                latest_line = line
    except Exception:
        pass

    if latest_line:
        try:
            # Expected Arduino output: "Quat: w, x, y, z"
            payload = latest_line.split(":")[1].split(",")
            w, x, y, z = [float(p.strip()) for p in payload]
            
            # OUTPUT TO TERMINAL
            print(f"QUAT DATA -> W: {w:+.4f} X: {x:+.4f} Y: {y:+.4f} Z: {z:+.4f}")
            sys.stdout.flush() 

            # scipy expects [x, y, z, w]
            current_quat = R_sci.from_quat([-y, z, -x, w])
        except Exception as e:
            print(f"Parse error: {e}")

    if now - last_update < UPDATE_INTERVAL:
        return
    last_update = now

    # Relative rotation calculation
    relative_quat = quat_offset.inv() * current_quat

    # Apply rotation matrix to model
    R = relative_quat.as_matrix()
    model.vertices = (R @ original_pts.T).T

    # Calculate Euler for UI display
    euler_display = relative_quat.as_euler('xyz', degrees=True)
    roll, pitch, yaw = euler_display

    new_info = (f" LIVE DATA (Press 'z' to Zero)\n"
                f" Roll:  {roll:+.2f}°\n"
                f" Pitch: {pitch:+.2f}°\n"
                f" Yaw:   {yaw:+.2f}°")
    msg.text(new_info)
    plt.render()

# --- REGISTER CALLBACKS & LAUNCH ---
plt.add_callback('key press', on_key)
plt.add_callback('timer', loop_func)
plt.timer_callback('start', dt=10)
plt.show(model, msg, interactive=True)

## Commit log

2025-02-19 PCB repo setup
    [BACK_QRE.kicad_pcb, BACK_QRE.kicad_sch, CONNECTIVITY.kicad_sch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]
2025-02-20 Schematic update
    [CONNECTIVITY.kicad_sch, MCU.kicad_sch, MECHANICS.kicad_sch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]
2025-02-21 HADES PCB Inspiration - just a file transfer
    [CONSMA001-ND.STEP, Connections.kicad_sch, Connections.sch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]
2025-02-21 HadesMicro and other PCBs with IMUs
    [HadesMicro.kicad_pcb, HadesMicro.kicad_sch]
2025-02-22 Force push
    [CONNECTIVITY.kicad_sch, MECHANICS.kicad_sch, MOTOR_CONTROL.kicad_sch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]
2025-02-24 MK V Schematic update
    [CONNECTIVITY.kicad_sch, MCU.kicad_sch, MECHANICS.kicad_sch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]
2025-02-27 Schematic update - finalized
    [CONNECTIVITY.kicad_sch, MCU.kicad_sch, MECHANICS.kicad_sch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]
2025-03-03 minor schematic update
    [SUMEC_MK_V.kicad_pcb]
2025-03-03 PCB update MKV
    [CONNECTIVITY.kicad_sch, MOTOR_CONTROL.kicad_sch, POWER_SUPPLY.kicad_sch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]
2025-03-04 minor pcb update
    [SUMEC_MK_V.kicad_pcb]
2025-03-04 PCB Updtae MK5
    [MECHANICS.kicad_sch, MOTOR_CONTROL.kicad_sch, POWER_SUPPLY.kicad_sch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]
2025-03-05 PCB and 3d update
    [MOTOR_CONTROL.kicad_sch, POWER_SUPPLY.kicad_sch, SENSORICS.kicad_sch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]
2025-03-05 PCB update - layout
    [SENSORICS.kicad_sch, SUMEC_MK_V.kicad_pcb]
2025-03-06 pcb routing
    [MOTOR_CONTROL.kicad_sch, POWER_SUPPLY.kicad_sch, SENSORICS.kicad_sch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]
2025-03-06 routing update
    [MOTOR_CONTROL.kicad_sch, POWER_SUPPLY.kicad_sch, SENSORICS.kicad_sch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]
2025-03-08 PCB pours update
    [SUMEC_MK_V.kicad_pcb]
2025-03-08 PCB Update, signal routing
    [MCU.kicad_sch, MOTOR_CONTROL.kicad_sch, POWER_SUPPLY.kicad_sch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]
2025-03-14 new step file
    [SUMEC_MK_V.kicad_pcb]
2025-03-17 pcb update
    [CONNECTIVITY.kicad_sch, MOTOR_CONTROL.kicad_sch, POWER_SUPPLY.kicad_sch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]
2025-03-19 PCB routing update
    [CONNECTIVITY.kicad_sch, MOTOR_CONTROL.kicad_sch, POWER_SUPPLY.kicad_sch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]
2025-03-23 a lot of routing and layout updates
    [CONNECTIVITY.kicad_sch, GRAPHICS.kicad_sch, MCU.kicad_sch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]
2025-03-25 sumec pcb update
    [CONNECTIVITY.kicad_sch, MCU.kicad_sch, MECHANICS.kicad_sch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]
2025-03-27 deletion of useless stuff
    [CONSMA001-ND.STEP, Connections.kicad_sch, Connections.sch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]
2025-03-28 SUMEC MKIV
    [MECHANICS.kicad_sch, MOTOR_CONTROL.kicad_sch, POWER_SUPPLY.kicad_sch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]
2025-03-30 silkscreen update
    [MECHANICS.kicad_sch, MOTOR_CONTROL.kicad_sch, POWER_SUPPLY.kicad_sch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]
2025-03-31 new qre board
    [CONNECTIVITY.kicad_sch, MCU.kicad_sch, MECHANICS.kicad_sch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]
2025-03-31 plotting + boms
    [CONNECTIVITY.kicad_sch, MCU.kicad_sch, MECHANICS.kicad_sch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]
2025-04-05 not sure what the update was but ill push it anywat bc ermm idk
    [Gyros-Scope.kicad_pcb, Gyros-Scope.kicad_sch, MK_IV bom.xlsx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]
2025-04-12 im gonna clean up this later
    [MOTOR_CONTROL.kicad_sch, POWER_SUPPLY.kicad_sch, SENSORICS.kicad_sch]
2025-04-15 gotta push it to the notebook
    [MOTOR_CONTROL.kicad_sch, POWER_SUPPLY.kicad_sch, SENSORICS.kicad_sch]
2025-04-24 MK5 bugfix fixed POL_L, minor changes, deleted nSLEEP and nFault connections to the MCU
    [CONNECTIVITY.kicad_sch, MCU.kicad_sch, MECHANICS.kicad_sch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]
2025-04-25 old things, but its better to have them
    [Additonal BOM mouser.xls, Additonal BOM.xlsx, COMPOUND.ipt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]
2025-04-26 old versions
    [100SP1T1B4M2QE.step, ESP32-WROOM-32D.step, EXTERNAL.kicad_sch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]
2025-04-28 MK5 changes and deletion of useless files
    [MCU.kicad_sch, MOTOR_CONTROL.kicad_sch, POWER_SUPPLY.kicad_sch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]
2025-05-15 schematic fixes
    [MCU.kicad_sch, MOTOR_CONTROL.kicad_sch, POWER_SUPPLY.kicad_sch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]
2025-05-21 Bom stuff
    [SUMEC_MK_V.xlsx]
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2026-03-01 updates to mk5
    [CONNECTIVITY.kicad_sch, MCU.kicad_sch, MECHANICS.kicad_sch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]
2026-03-13 MK5 PCB rework
    [CONNECTIVITY.kicad_sch, MCU.kicad_sch, MOTOR_CONTROL.kicad_sch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]
2026-03-31 MK5 new update of the PCB
    [CONNECTIVITY.kicad_sch, GRAPHICS.kicad_sch, MCU.kicad_sch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]
2026-04-07 silkscreen update and PCB plot
    [SUMEC_MK_V-B_Cu.gbl, SUMEC_MK_V-B_Mask.gbs, SUMEC_MK_V-B_Paste.gbp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]
2026-04-10 new MK5.5 update
    [SUMEC_MK_V-B_Cu.gbl, SUMEC_MK_V-B_Mask.gbs, SUMEC_MK_V-B_Paste.gbp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]
2026-04-10 rename of mk5.1 version, renamed to mk5 pro
    [MK_V_mouser.xls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]
2026-04-11 Rename schematic project to SUMEC_MK_V_Pro
    Update main_hw/SUMEC_MK_V_Pro/SUMEC_MK_V_Pro.kicad_sch: replace project references from "SUMEC_MK_V" to "SUMEC_MK_V_Pro" across many instances so component references match the renamed project. This ensures the schematic's instance metadata reflects the new project name.
    [SUMEC_MK_V_Pro.kicad_sch]
2026-04-11 Update KiCad PCB render_cache polygons
    Added missing paths: 3V3 for JP3, GND for C1. Minor path optimization was provided.
2026-04-11 Rename sheet reference to SUMEC_MK_V_Pro
    Update the KiCad project file to reference the Pro schematic sheet: changed the sheets entry from "SUMEC_MK_V" to "SUMEC_MK_V_Pro" in SUMEC_MK_V_Pro.kicad_pro to keep the project configuration consis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
2026-04-12 Update SUMEC_MK_V_Pro.kicad_pcb
    Paths redesign: Net-(JP3-A), Net-(U7-RESET), 3V3 and 12V on In2 layer,
2026-04-12 Update SUMEC_MK_V_Pro.kicad_sch
    Added description for PS1 and PS0 pins of BN055 IMU onboard sensor.
    [SUMEC_MK_V_Pro.kicad_sch]
2026-04-12 Update SUMEC_MK_V_Pro.kicad_sch
    Added description for COM3 pin of BN055 for I2C address selection.
    [SUMEC_MK_V_Pro.kicad_sch]
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2026-04-13 Bom update
    [MK_IV bom.xlsx, SUMEC_MK_V_Pro.xlsx]
2026-04-13 Brought unchanged MK5 back
    Brought the deleted MK5 back
    [CONNECTIVITY.kicad_sch, GRAPHICS.kicad_sch, MCU.kicad_sch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]
2026-04-13 SUMEC Mk5 Pro bom update
    [MK_V_mouser.xls, SUMEC_MK_V.xlsx, SUMEC_MK_V_Pro.kicad_sch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]
2026-04-15 Bom update and cleanup
    [MK_V_pro_mouser.xls, SUMEC_MK_V.xlsx, SUMEC_MK_V_Pro.xlsx]
2026-04-27 Final update for MK Pro
    PCB, schematic update, IMU software
    [QRE_MiniBoard-V2.step, QRE_MiniBoardV2.kicad_pcb, QRE_MiniBoardV2.step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]
2026-05-06 Prepare for release
    [MK_V_mouser.xls, SUMEC_MK_V.xlsx, SUMEC_MK_V_Pro.kicad_sch]
